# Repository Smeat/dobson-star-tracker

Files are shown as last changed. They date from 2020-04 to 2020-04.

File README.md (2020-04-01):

# dobson-star-tracker
This project aims to enable makers to motorize their dobson-style mounted telescopes using easily sourced hardware.

## Hardware

+ 2 Stepper Motors + drivers. I found that the size of my telescope (as pictured badly below) requires at least NEMA 17 with 1.2A current per phase. The altitude motor uses a (roughly) 5:1 gear ratio
+ Arduino with at least 6 Digital Pins. The instructions and example config work for an Arduino Mega with a RAMPS 1.4 shield
+ 3D printed motor mounts and gears
+ Optional: Two Buttons; Each requires one additional digital pin
+ Optional: A GPS module; Requires either a free TX/RX pin pair or two digital pins

## 3D Files

The printable files (stl and step format) can be found at: https://www.thingiverse.com/thing:3851307

## Installation

First of all, you will need the [Arduino IDE](https://www.arduino.cc/) and a few libraries:

* [TimerOne (on the Arduino Mega)](https://github.com/PaulStoffregen/TimerOne)
* [DueTimer (on the Arduino Due)](https://github.com/ivanseidel/DueTimer)
* [AccelStepper](https://www.airspayce.com/mikem/arduino/AccelStepper/)
* [FuGPS (should work without, if no GPS module is installed)](https://github.com/fu-hsi/FuGPS)
* [TimeLib](https://github.com/PaulStoffregen/Time)

Clone or download this repository and open the dobson-star-tracker.ino file in the Arduino IDE. The first thing you will need to set up are a few constants in the config.h file. Please read through the whole file and set everything according to your needs. When you initially build and upload the sketch without setting at least the `AZ_STEPS_PER_REV`and `ALT_STEPS_PER_REV` constants, the scope will not move since both of the values are set to 0. This is done to prevent the motors from moving unexpectedly and maybe damaging your telescope. Check the output of the Serial Monitor for more information. Initially, `DEBUG`, `DEBUG_SERIAL` and `DEBUG_STOP_ON_CONFIG_INSANITY` are enabled for useful output via the Serial Monitor. Once everything works correctly, you can disable them. For more information on how to connect the scope to Stellarium or how to use the display unit, check below.

## Connection to Stellarium

There are a few requisites for establishing a connection between the telescope and Stellarium.

### Arduino project
1. Set the `SERIAL_BAUDRATE` to 9600
2. Disable all of the DEBUG constants, so that the telescope does not send invalid commands to Stellarium. If Stellarium receives an invalid answer, it will wait for a few seconds before interacting with the telescope again. This either means, that it won't receive position updates from the telescope or that it won't send your commands. Setting a new position requires three commands sent by Stellarium. If one of them receives an invalid answer, Stellarium will not send the rest of the commands and your input will basically be ignored.
3. Close the Serial Monitor or Stellarium will not be able to connect to the telescope

### Settings in Stellarium
1. Open Stellarium and locate the "Telescope" tab. It should be in the lower control bar to the left of the time controls. If you can't find it, you may need to enable the "Telescope Control" plugin and restart Stellarium. Do so in the Configuration window in the last tab.
2. Click "Add" and set the following:
    * **Telescope controlled by:** "Stellarium, directly through a serial port"
    * **Name:** Choose one :)
    * **Connection delay:** Something around 0,1s, but should not matter too much
    * **Coordinate System:** J2000 (default)
    * **Start/Connect at startup:** Ticking the box means that Stellarium will try to connect to the telescope as soon as you open it. Use your preference.
    * **Serial port:** Select the same port as in your Arduino IDE
    * **Device Model:** Meade LX200 (compatible)
    * **Use field of view indicators:** Does not matter for controlling the telescope. Use your preference.
3. Confirm the settings with "OK"
4. Use "Start" to connect to the telescope
5. Wait a few seconds for it to show up on the screen and for it to settle down
6. The motors will not move until you align the telescope. To do so, follow this procedure:
   1. Choose your alignment star and select it in Stellarium
   2. Click "current object" in the telescope section
   3. Manually point the telescope at the selected star
   3. Confirm alignment by clicking "slew" and wait for the telescope on screen to point at the correct star
   4. The telescope is now aligned to that particular star and the stepper motors will be enabled
7. Now you can select a different star in Stellarium
8. Click "current object" in the telescope section
9. Click "slew" and watch the telescope move

## Wiring a RAMPS1.4

Wiring without the display unit

## Wiring with the Display Unit

My example uses a version of the well-known [RepRap Discount Full Graphics Smart Controller](https://reprap.org/wiki/RepRapDiscount_Full_Graphic_Smart_Controller). The only connection between the two Arduino boards is via the two cables connected to RX2 and TX2 on the Display Unit. For more information + code for the display unit head over to [ThisIsJustARandomGuy/telescope-display-unit/](https://github.com/ThisIsJustARandomGuy/telescope-display-unit/).

Wiring without the display unit

# Aligning using the display unit

If you have a display unit, you can use it to easily align the telescope. This works with/without Stellarium. To align the telescope when using a display unit, do the following:

1. Start the display unit and scope
2. Navigate to "Set Alignment" -> "Stars"
3. Look through the list and select a star that's visible in the sky
4. Once you click the star in the list, the motors of the telescope will turn off
5. Align the telescope to the star you have selected
6. Click again and confirm the alignment
7. The motors will turn on again and the telescope is now aligned.

## Serial Commands

+ :HLP# Print available Commands
+ Commands used by stellarium (you can use them as well)
  + :GR# Get Right Ascension
  + :GD# Get Declination
  + :Sr,HH:MM:SS# Set Right Ascension; Example: :Sr,12:34:56#
  + :Sd,[+/-]DD:MM:SS# Set Declination (DD is degrees) Example: :Sd,+12:34:56#
  + :MS# Start Move
  + :Q# Quit Move (Not Implemented)
+ Other commands
  + :TRK0# Disable tracking. This sets the telescopes isHomed member variable to false, so the motors stop moving
  + :TRK1# Enable tracking. The telescope will track whatever the target is
  + :STP0# Disable steppers permanently
  + :STP1# Enable steppers (after they were disabled using the STP0 command)
+ Debug commands
  + :DBGDSP# Send a status update to the display unit
  + :DBGDM[00-99]# Disable Motors for XX seconds
  + :DBGM[0-9]# Move to debug position X (see conversion.cpp; Later we will have a separate file with a star catalogue)
  + :DBGMIA# Increase Right Ascension by 1 degree
  + :DBGMDA# Decrease Right Ascension by 1 degree
  + :DBGMID# Increase Declination by 1 degree
  + :DBGMDD# Decrease Declination by 1 degree

## TODOs

The Most important TODOs are as follows (in no particular order)
+ Documentation
+ Equatorial Mounts: Adding equatorial mounts would be rather easy, but I don't own one so it's difficult to test. Maybe someone is interested in providing a PR?
+ Board compatibility: Out-of-the-box support for Arduino Mega and Arduino Due with their respective RAMPS shields (Mostly done, Mega + RAMPS 1.4 and Due + modified RAMPS 1.4 work)
+ Time keeping: Handle big swings which could happen due to GPS issues
+ EEPROM: Store time and location in EEPROM (Mega) or Flash (Due); Provide a simple API for doing so
+ Motor control: Turn On/Off permanently. Off for X seconds is already implemented as :DBGDM[00-99]#
+ SD card support: Loading a star atlas from a sd card (preferrably connected to the display unit, but direct connection should be possible too)

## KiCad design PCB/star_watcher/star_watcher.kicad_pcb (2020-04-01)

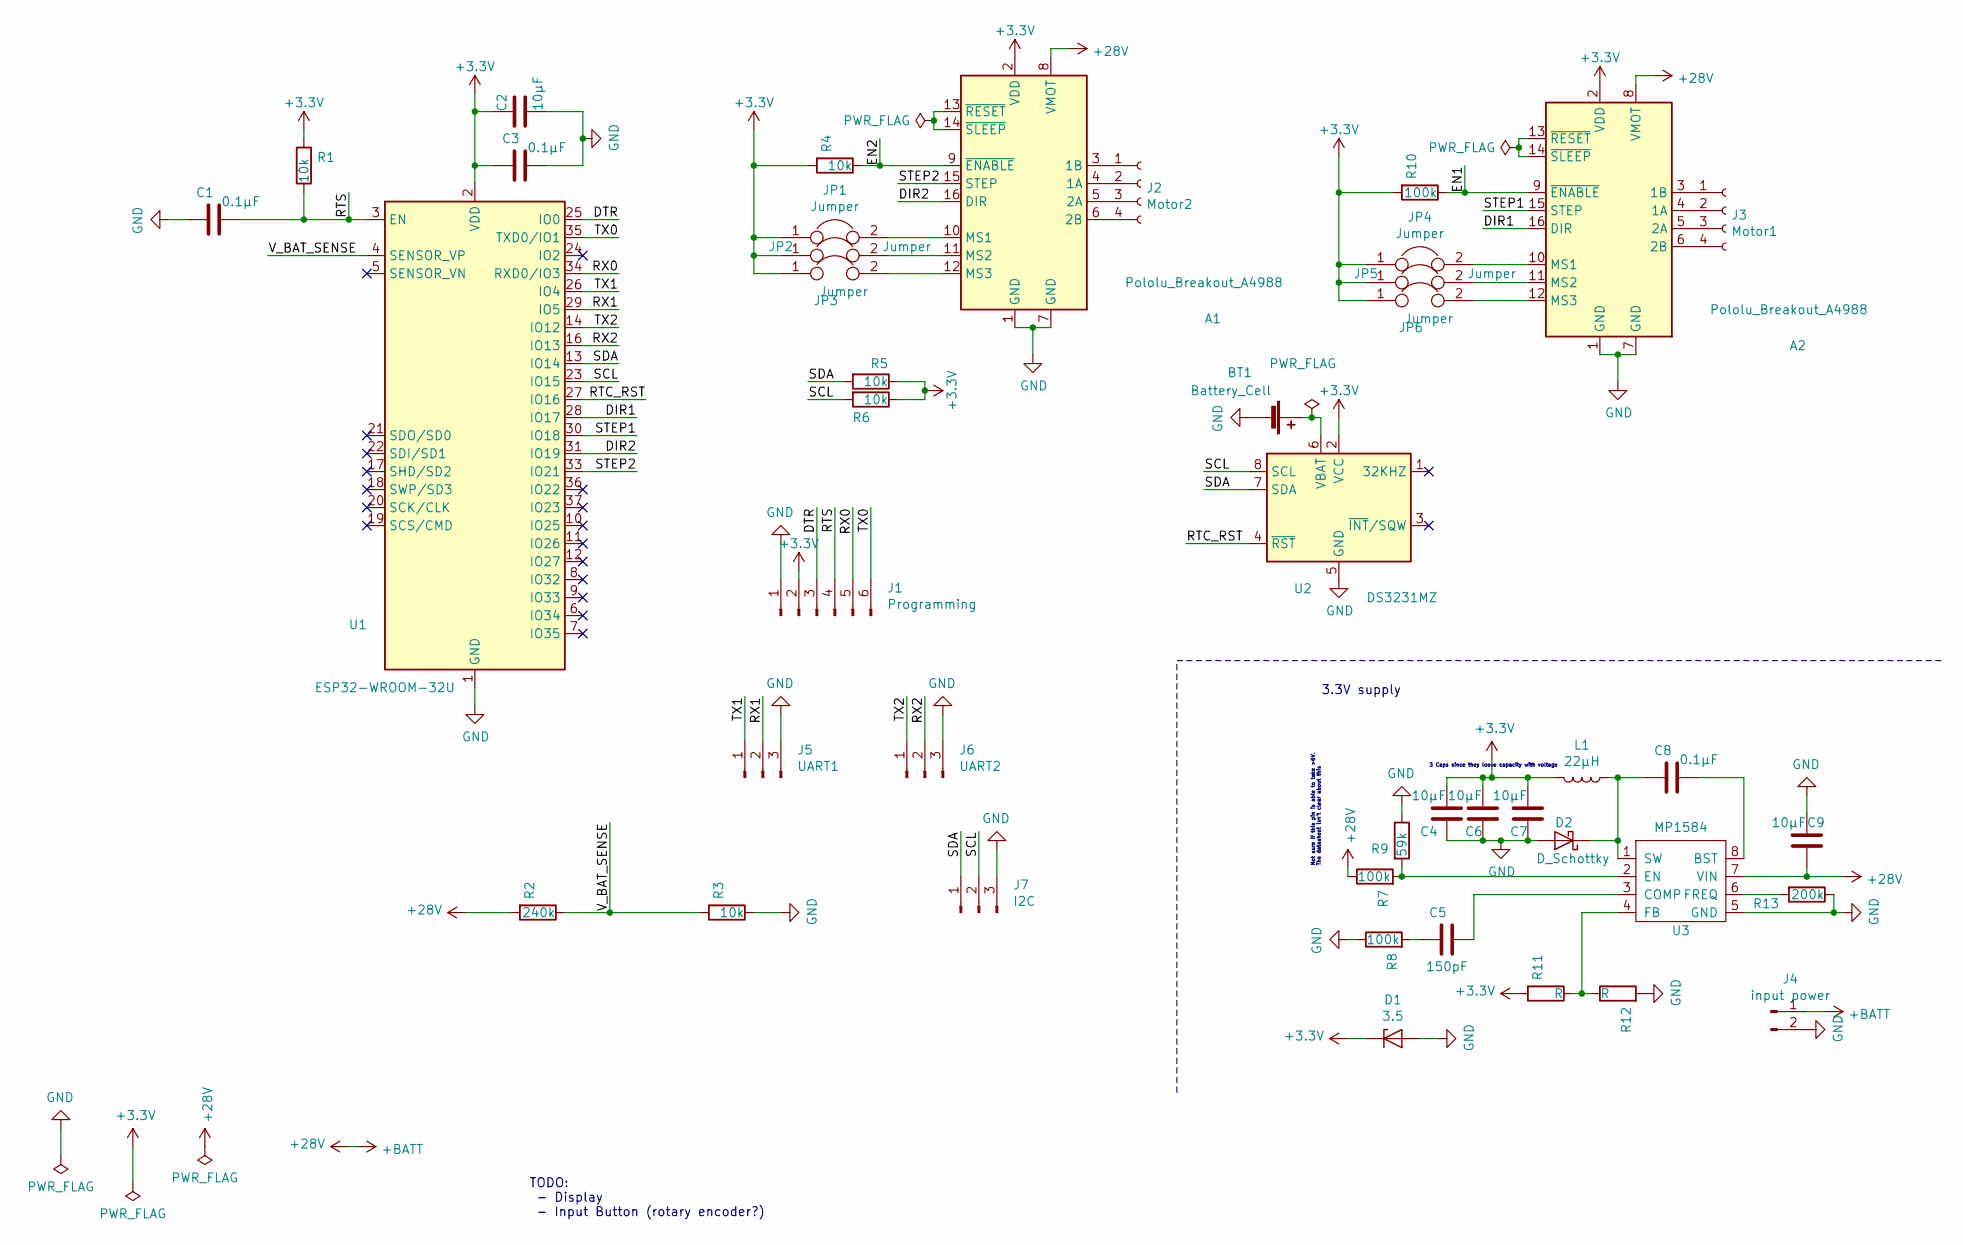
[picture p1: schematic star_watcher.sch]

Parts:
A1, A2: Pololu_Breakout_A4988; Pololu_Breakout-16_15.2x20.3mm
BT1: Battery_Cell; BatteryHolder_Keystone_103_1x20mm
C1, C3, C8: 0.1µF; C_0603_1608Metric
C2, C4, C6, C7, C9: 10µF; C_0805_2012Metric
C5: 150pF; C_0603_1608Metric
D1: 3.5; D_MELF
D2: D_Schottky; D_SMA
J1: Programming; PinHeader_1x06_P2.54mm_Vertical
J2: Motor2; PinHeader_1x04_P2.54mm_Vertical
J3: Motor1; PinHeader_1x04_P2.54mm_Vertical
J4: input power; SolderWirePad_1x02_P7.62mm_Drill2.5mm
J5: UART1; PinHeader_1x03_P2.54mm_Vertical
J6: UART2; PinHeader_1x03_P2.54mm_Vertical
J7: I2C; PinHeader_1x03_P2.54mm_Vertical
JP1, JP2, JP3, JP4, JP5, JP6: Jumper; PinHeader_1x02_P2.54mm_Vertical
L1: 22µH; L_12x12mm_H6mm
R1, R3, R4, R5, R6: 10k; R_0805_2012Metric
R2: 240k; R_0805_2012Metric
R7, R8, R10: 100k; R_0805_2012Metric
R9: 59k; R_0805_2012Metric
R11, R12: R; R_0805_2012Metric
R13: 200k; R_0805_2012Metric
U1: ESP32-WROOM-32U; ESP32-WROOM-32
U2: DS3231MZ; SOIC-8_3.9x4.9mm_P1.27mm
U3: MP1584; SOIC-8_3.9x4.9mm_P1.27mm

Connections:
+3V3: A1.2 (VDD), A2.2 (VDD), C2.1, C3.2, C4.2, C6.2, C7.2, D1.1 (K), J1.2, JP1.1, JP2.1, JP3.1, JP4.1, JP5.1, JP6.1, L1.2, R1.2, R4.2, R5.1, R6.1, R10.2, R11.2, U1.2 (VDD), U2.2 (VCC)
+28V: A1.8 (VMOT), A2.8 (VMOT), C9.1, J4.1, R2.2, R7.1, U3.7 (VIN)
/DIR1: A2.16 (DIR), U1.28 (IO17)
/DIR2: A1.16 (DIR), U1.31 (IO19)
/DTR: J1.3, U1.25 (IO0)
/EN1: A2.9 (~ENABLE), R10.1
/EN2: A1.9 (~ENABLE), R4.1
/RTC_RST: U1.27 (IO16), U2.4 (~RST)
/RTS: C1.1, J1.4, R1.1, U1.3 (EN)
/RX0: J1.5, U1.34 (RXD0/IO3)
/RX1: J5.2, U1.29 (IO5)
/RX2: J6.2, U1.16 (IO13)
/SCL: J7.2, R6.2, U1.23 (IO15), U2.8 (SCL)
/SDA: J7.1, R5.2, U1.13 (IO14), U2.7 (SDA)
/STEP1: A2.15 (STEP), U1.30 (IO18)
/STEP2: A1.15 (STEP), U1.33 (IO21)
/TX0: J1.6, U1.35 (TXD0/IO1)
/TX1: J5.1, U1.26 (IO4)
/TX2: J6.1, U1.14 (IO12)
/V_BAT_SENSE: R2.1, R3.2, U1.4 (SENSOR_VP)
GND: A1.1 (GND), A1.7 (GND), A2.1 (GND), A2.7 (GND), BT1.2 (-), C1.2, C2.2, C3.1, C4.1, C6.1, C7.1, C9.2, D1.2 (A), D2.2 (A), J1.1, J4.2, J5.3, J6.3, J7.3, R3.1, R8.1, R9.1, R12.2, R13.1, U1.1 (GND), U1.15 (GND), U1.38 (GND), U1.39 (GND), U2.5 (GND), U3.5 (GND)
unnamed: A1.3 (1B), J2.1
unnamed: A1.4 (1A), J2.2
unnamed: A1.5 (2A), J2.3
unnamed: A1.6 (2B), J2.4
unnamed: A1.10 (MS1), JP1.2
unnamed: A1.11 (MS2), JP2.2
unnamed: A1.12 (MS3), JP3.2
unnamed: A1.13 (~RESET), A1.14 (~SLEEP)
unnamed: A2.3 (1B), J3.1
unnamed: A2.4 (1A), J3.2
unnamed: A2.5 (2A), J3.3
unnamed: A2.6 (2B), J3.4
unnamed: A2.10 (MS1), JP4.2
unnamed: A2.11 (MS2), JP5.2
unnamed: A2.12 (MS3), JP6.2
unnamed: A2.13 (~RESET), A2.14 (~SLEEP)
unnamed: BT1.1 (+), U2.6 (VBAT)
unnamed: C5.1, U3.3 (COMP)
unnamed: C5.2, R8.2
unnamed: C8.1, U3.8 (BST)
unnamed: C8.2, D2.1 (K), L1.1, U3.1 (SW)
unnamed: R7.2, R9.2, U3.2 (EN)
unnamed: R11.1, R12.1, U3.4 (FB)
unnamed: R13.2, U3.6 (FREQ)

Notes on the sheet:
Not sure if this pin is able to take >6V. The datasheet isn't clear about this
3 Caps since they loose capacity with voltage
3.3V supply
TODO: - Display - Input Button (rotary encoder?)

Board: 2 copper layers, 44 parts (4 on the bottom side), 45 nets, no tracks yet.

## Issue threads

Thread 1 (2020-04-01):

TODO

Smeat, 2020-04-01:
- [ ] Add interface for getting gps/time from phone via bluetooth/wifi
- [ ] Connection to Stellarium and KStars via wifi
- [x] Schematic
  -  [X] Find a display with red background light
     - The LEDs on the Nokia 5110 LCD can easily be replaced
  -  [ ] SD support for saving star maps
   - [ ] Implement filesystem or use a faster fat lib
      - Fat reads were at 0.5MB/s. RAW at 7MB/s
         - SIMBAD library for Vmag <11 is about 16mb for the data and 30mb for the names
      - [ ] UI for selecting targets, calibrating etc
- [ ]  Actually get the hardware and test it

Smeat, 2020-04-11:
Using another project: https://github.com/Smeat/Star_Tracker

Closed 2020-04-11.

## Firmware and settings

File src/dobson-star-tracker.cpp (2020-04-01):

#include <TimeLib.h>
#include <AccelStepper.h>
#include <Arduino.h>
#include <HardwareSerial.h>
#include <MultiStepper.h>

#include "config.h"
#include "conversion.h"
//#include "location.h"

//Load the timer library, depending on the selected BOARD_TYPE
#ifdef BOARD_ARDUINO_MEGA
	#include <TimerOne.h>
#elif defined BOARD_ARDUINO_DUE
	#include <DueTimer.h>
#endif

// Load the display unit if it's enabled
#ifdef SERIAL_DISPLAY_ENABLED
#include "display_unit.h"
#endif

// Load the required observer class
#ifdef GPS_FIXED_POS
	#include "./FixedObserver.h"
#else
	#include "./GpsObserver.h"
#endif

// Include the mount, depending on the selected MOUNT_TYPE
#ifdef MOUNT_TYPE_DOBSON
	#include "./Dobson.h"
#elif defined MOUNT_TYPE_EQUATORIAL
	#include "./Equatorial.h" // NOT IMPLEMENTED!
#elif defined MOUNT_TYPE_DIRECT
	#include "./DirectDrive.h"
#endif


// Initialize the Steppers
AccelStepper azimuth(AccelStepper::DRIVER, AZ_STEP_PIN, AZ_DIR_PIN);    // Azimuth stepper
AccelStepper altitude(AccelStepper::DRIVER, ALT_STEP_PIN, ALT_DIR_PIN); // Altitude stepper

// Initialize the Observer (either fixed or GPS)
#ifdef GPS_FIXED_POS
	FixedObserver observer(ALT, LAT, LNG, INITIAL_YEAR, INITIAL_MONTH, INITIAL_DAY, INITIAL_HOUR, INITIAL_MINUTE, INITIAL_SECOND);
#else
	GpsObserver observer;
#endif

// Initialize the Mount
#ifdef MOUNT_TYPE_DOBSON
	Dobson scope(azimuth, altitude, observer);
#elif defined MOUNT_TYPE_EQUATORIAL
	Equatorial scope(azimuth, altitude, observer); // NOT IMPLEMENTED!
#elif defined MOUNT_TYPE_DIRECT
	DirectDrive scope(azimuth, altitude, observer);
#endif

// Are the stepper drivers currently enabled?
bool motorsEnabled = false;

// This increases every loop iteration and resets at 10.000
unsigned int loopIteration = 0;

// Is the loop() function being run for the first time?
bool first_loop_run = true;

// millis() at the time of the latest call to Mount::calculateMotorTargets()
long last_motor_update = 0;

#ifdef DEBUG_HOME_IMMEDIATELY
	const bool homeImmediately = true;
#else
	const bool homeImmediately = false;
#endif


/**
 * Motor Interrupt handler
 * This is attached to timer interrupt 1. It gets called every STEPPER_INTERRUPT_FREQ / 1.000.000 seconds and moves our steppers
 */
void moveSteppers() {
	azimuth.run();
	altitude.run();
}


/**
 * Initialize stepper drivers. Sets pin inversion config, max speed and acceleration per stepper
 */
void setupSteppers() {
	// Set stepper pins
	pinMode(AZ_ENABLE_PIN, OUTPUT);  // Azimuth pin
	pinMode(ALT_ENABLE_PIN, OUTPUT); // Altitude pin

	azimuth.setPinsInverted(true, false, false);
	azimuth.setMaxSpeed(AZ_MAX_SPEED);
	azimuth.setAcceleration(AZ_MAX_ACCEL);

	altitude.setPinsInverted(true, false, false);
	altitude.setMaxSpeed(ALT_MAX_SPEED);
	altitude.setAcceleration(ALT_MAX_ACCEL);

	// Setup the stepper interrupt. Depends on the selected board
#ifdef BOARD_ARDUINO_MEGA
	Timer1.initialize(STEPPER_INTERRUPT_FREQ);
	Timer1.attachInterrupt(&moveSteppers);
#elif defined BOARD_ARDUINO_DUE
	Timer.getAvailable()
		.attachInterrupt(&moveSteppers)
		.start(STEPPER_INTERRUPT_FREQ);
#elif defined(BOARD_ESP32)
	hw_timer_t * timer = NULL;
	// Use 1st timer of 4 (counted from zero).
	// Set 80 divider for prescaler (see ESP32 Technical Reference Manual for more
	// info).
	timer = timerBegin(0, 80, true);

	// Attach onTimer function to our timer.
	timerAttachInterrupt(timer, &moveSteppers, true);

	// Set alarm to call onTimer function every second (value in microseconds).
	// Repeat the alarm (third parameter)
	timerAlarmWrite(timer, STEPPER_INTERRUPT_FREQ, true);

	// Start an alarm
	timerAlarmEnable(timer);
#endif

	DEBUG_PRINT("  Steppers enabled:  ");
#ifdef AZ_ENABLE
	DEBUG_PRINT("Az=ON");
#else
	DEBUG_PRINT("Az=OFF");
#endif

#ifdef ALT_ENABLE
	DEBUG_PRINTLN("  Alt=ON");
#else
	DEBUG_PRINTLN("  Alt=OFF");
#endif
} // setupSteppers


/*
 * This function turns stepper motor drivers on, if these conditions are met:
 * STEPPERS_ON_PIN reads HIGH
 * operating mode is not Mode::INITIALIZING
 * TODO Maybe the conditions need to change (esp. the opmode one)
 */
void setSteppersOnOffState() {
	const bool isTracking = scope.getMode() == Mode::TRACKING;

#ifdef STEPPERS_ON_PIN
	// If the STEPPERS_ON switch is installed, check its state
	const bool steppersSwitchOn = digitalRead(STEPPERS_ON_PIN) == HIGH;
#else
	// If no STEPPERS_ON switch is installed, define its state as enabled
#define steppersSwitchOn true
#endif

	if (steppersSwitchOn && isTracking) {
		// Motors on
		motorsEnabled = true;
#ifdef AZ_ENABLE
		digitalWrite(AZ_ENABLE_PIN, LOW);
#endif
#ifdef ALT_ENABLE
		digitalWrite(ALT_ENABLE_PIN, LOW);
#endif
	}
	else {
		// Motors OFF
		motorsEnabled = false;
#ifdef AZ_ENABLE
		digitalWrite(AZ_ENABLE_PIN, HIGH);
#endif
#ifdef ALT_ENABLE
		digitalWrite(ALT_ENABLE_PIN, HIGH);
#endif
	}
}

#ifndef REMOVE_SPLASH
	void greet() {
		DEBUG_PRINTLN("                      __          __  _                          ");
		DEBUG_PRINTLN("                      \\ \\        / / | |                         ");
		DEBUG_PRINTLN("                       \\ \\  /\\  / /__| | ___ ___  _ __ ___   ___ ");
		DEBUG_PRINTLN("                        \\ \\/  \\/ / _ \\ |/ __/ _ \\| '_ ` _ \\ / _ \\");
		DEBUG_PRINTLN("                         \\  /\\  /  __/ | (_| (_) | | | | | |  __/");
		DEBUG_PRINTLN("                          \\/  \\/ \\___|_|\\___\\___/|_| |_| |_|\\___|");
		DEBUG_PRINTLN("                                                                 ");

		DEBUG_PRINTLN(" _____        _                          _____ _                _______             _             ");
		DEBUG_PRINTLN("|  __ \\      | |                        / ____| |              |__   __|           | |            ");
		DEBUG_PRINTLN("| |  | | ___ | |__  ___  ___  _ __     | (___ | |_ __ _ _ __      | |_ __ __ _  ___| | _____ _ __ ");
		DEBUG_PRINTLN("| |  | |/ _ \\| '_ \\/ __|/ _ \\| '_ \\     \\___ \\| __/ _` | '__|     | | '__/ _` |/ __| |/ / _ \\ '__|");
		DEBUG_PRINTLN("| |__| | (_) | |_) \\__ \\ (_) | | | |    ____) | || (_| | |        | | | | (_| | (__|   <  __/ |   ");
		DEBUG_PRINTLN("|_____/ \\___/|_.__/|___/\\___/|_| |_|   |_____/ \\__\\__,_|_|        |_|_|  \\__,_|\\___|_|\\_\\___|_|   ");
		DEBUG_PRINTLN("                                                                                               ");

		DEBUG_PRINTLN("Welcome to the dobson-star-tracker serial console.");
		DEBUG_PRINTLN("Before continuing, please set up the config.h file.");
		DEBUG_PRINTLN("Type :HLP# and press Enter to see a list of available commands");
		DEBUG_PRINTLN();
		DEBUG_PRINTLN();
		DEBUG_PRINTLN();
	}
#endif


/**
 * Performs a few sanity checks on the config. If there are any obvious errors,
 * warn the user. Depending on what is set in config.h this may enter an
 * endless loop to prevent damage to the telescope hardware. Have a look at
 * DEBUG_STOP_ON_CONFIG_INSANITY in config.h
 */
void config_sanity_check() {
	bool failed = false;
	bool can_continue = true;

	// Begin checks
	if (AZ_STEPS_PER_REV <= 0) {
		DEBUG_PRINTLN("  Warning: AZ_STEPS_PER_REV should probably be > 0");
		failed = true;
	}
	if (ALT_STEPS_PER_REV <= 0) {
		DEBUG_PRINTLN("  Warning: ALT_STEPS_PER_REV should probably be > 0");
		failed = true;
	}

	#if defined BUZZER_PIN
		#if BUZZER_PIN == STEPPERS_ON_PIN
			DEBUG_PRINTLN("  Error: BUZZER_PIN and STEPPERS_ON_PIN are set to the same pin number.");
			failed = true; can_continue = false;
		#endif
		#if BUZZER_PIN == HOME_NOW_PIN
			DEBUG_PRINTLN("  Error: BUZZER_PIN and HOME_NOW_PIN are set to the same pin number.");
			failed = true; can_continue = false;
		#endif
		#if BUZZER_PIN == TARGET_SELECT_PIN
			DEBUG_PRINTLN("  Error: BUZZER_PIN and TARGET_SELECT_PIN are set to the same pin number.");
			failed = true; can_continue = false;
		#endif
	#endif

	#if defined STEPPERS_ON_PIN
		#if STEPPERS_ON_PIN == HOME_NOW_PIN
			DEBUG_PRINTLN("  Error: STEPPERS_ON_PIN and HOME_NOW_PIN are set to the same pin number.");
			failed = true; can_continue = false;
		#endif
		#if STEPPERS_ON_PIN == TARGET_SELECT_PIN
			DEBUG_PRINTLN("  Error: STEPPERS_ON_PIN and TARGET_SELECT_PIN are set to the same pin number.");
			failed = true; can_continue = false;
		#endif
	#endif

	#if defined HOME_NOW_PIN && HOME_NOW_PIN == TARGET_SELECT_PIN
		DEBUG_PRINTLN("  Error: HOME_NOW_PIN and TARGET_SELECT_PIN are set to the same pin number.");
		failed = true; can_continue = false;
	#endif

	#ifndef GPS_FIXED_POS
		#if GPS_MIN_SATELLITES <= 0
			DEBUG_PRINTLN("  Warning: GPS_MIN_SATELLITES should probably be > 0");
			failed = true;
		#endif

		#if GPS_MIN_SATELLITES_TIME <= 0
			DEBUG_PRINTLN("  Warning: GPS_MIN_SATELLITES_TIME should probably be > 0");
			failed = true;
		#endif
	#endif

	#if UPDATE_MOTOR_POS_MS <= 0
		DEBUG_PRINTLN("  Warning: UPDATE_MOTOR_POS_MS should probably be > 0");
		failed = true;
	#endif
		

	#if STEPPER_INTERRUPT_FREQ <= 0
		DEBUG_PRINTLN("  Warning: STEPPER_INTERRUPT_FREQ should probably be > 0");
		failed = true;
	#endif

	// End checks

	if (failed) {
		DEBUG_PRINTLN("  Config sanity check has failed.");
		DEBUG_PRINTLN("  Check the output above for errors and review config.h");
		DEBUG_PRINTLN("  Do not continue until you know why this message appeared!");
		#ifdef DEBUG_STOP_ON_CONFIG_INSANITY
			bool stop = true;
			while (stop) {
				// Buzzer is installed. Start buzzing and continue endless loop
				#ifdef BUZZER_PIN
					digitalWrite(BUZZER_PIN, HIGH);
				#endif

				// DEBUG_SERIAL is enabled. Wait for "ok" input
				#ifdef DEBUG_SERIAL
					DEBUG_PRINTLN("  Press 1 and Enter to continue");
					while (!Serial.available()) {}
					if (Serial.read() == '1') {
						if (can_continue) {
							stop = false;
						}
						else {
							DEBUG_PRINTLN("  I'm sorry Dave, I'm afraid I can't do that. Please fix the errors first");
						}
					}
				#endif
			}
			// Buzzer is installed. Stop buzzing after the continue command
			#ifdef BUZZER_PIN
				digitalWrite(BUZZER_PIN, LOW);
			#endif
		#endif
	}
}

/**
 * Run various tasks required to initialize the following:
 * Serial connection
 * Serial communication
 * Stepper motors
 * If enabled:
 *     Display module
 *     GPS module
 *     Buzzer
 *     Steppers On/Off Button
 *     Home Now Button
 *     Target Select Button
 *
 * Finally, telescope.initialize() is called. This sets an initial target (depending on the MOUNT_TYPE) and the initial scope operating mode
 */
void setup() {
	Serial.begin(SERIAL_BAUDRATE);
	#if defined DEBUG && defined DEBUG_SERIAL
		delay(500);
		#ifndef REMOVE_SPLASH
			greet();
		#endif
	#endif
			delay(500);
	DEBUG_PRINTLN("> Performing config sanity check");
	config_sanity_check();
	
	// If the serial display is enabled, begin communicating with it
	#ifdef SERIAL_DISPLAY_ENABLED
		DEBUG_PRINT("> Initializing Display module ... ");
		initDisplayCommunication(scope);
		DEBUG_PRINTLN("done");
	#else
		DEBUG_PRINTLN("Display module is disabled");
	#endif

	DEBUG_PRINT("> Initializing Observer module ... ");
	// This initializes the Observer (including the GPS module, if required)
	observer.initialize();
	DEBUG_PRINTLN("done");
	#if defined DEBUG && defined DEBUG_SERIAL
		observer.printDebugInfo();
	#endif

	DEBUG_PRINTLN("> Initializing Telescope module ... ");
	// Initialize the telescope
	scope.initialize();

	DEBUG_PRINTLN();
	DEBUG_PRINTLN("> Initializing Serial communications module ... ");
	// This sets up communication with Stellarium / Serial console
	initCommunication(scope);

	DEBUG_PRINTLN();
	DEBUG_PRINTLN("> Initializing Stepper drivers ... ");
	// Initialize stepper motor drivers
	setupSteppers();

	DEBUG_PRINTLN("> Initializing Buttons and Output ... ");
	DEBUG_PRINT("    Buzzer...............");
	// Button pins
	#ifdef BUZZER_PIN
		pinMode(BUZZER_PIN, OUTPUT);
		digitalWrite(BUZZER_PIN, HIGH);
		//delay(1000);
		digitalWrite(BUZZER_PIN, LOW);
		DEBUG_PRINLN("done");
	#else
		DEBUG_PRINTLN("not connected");
	#endif

	DEBUG_PRINT("    Steppers on/off......");
	// Steppers on/off switch
	#ifdef STEPPERS_ON_PIN
		pinMode(STEPPERS_ON_PIN, INPUT);
		DEBUG_PRINLN("done");
	#else
		DEBUG_PRINTLN("not connected");
	#endif


	DEBUG_PRINT("    Home now.............");
	// Home now switch
	#ifdef HOME_NOW_PIN
		pinMode(HOME_NOW_PIN, INPUT);

		DEBUG_PRINLN("done");
	#else
		DEBUG_PRINTLN("not connected");
	#endif


	DEBUG_PRINT("    Debug target.........");
	// Target select pin
	#ifdef TARGET_SELECT_PIN
		// Input mode for the select pin is INPUT with PULLUP enabled, so that we can use a longer cable
		pinMode(TARGET_SELECT_PIN, INPUT_PULLUP);
		DEBUG_PRINLN("done");
	#else
		DEBUG_PRINTLN("not connected");
	#endif

	// If the serial display is enabled, send the telescope status
	#ifdef SERIAL_DISPLAY_ENABLED
		DEBUG_PRINTLN("> Sending status to Display .... ");
		display_statusUpdate(scope);
	#endif

	DEBUG_PRINTLN("> Initialization done");
	DEBUG_PRINTLN();
	DEBUG_PRINTLN();
	DEBUG_PRINTLN();

}


/*
 * Main program loop. It does roughly the following (in order)
 * 1) Check whether the Home Button is pressed. If so, set the scope back to homing mode
 * 2) Get updates from the GPS module and tell the telescope instance about it
 * 3) Handle communication over serial
 * 4) Check whether homing mode should end (TODO This should move to the telescope class)
 * 5) Turn the stepper drivers on/off
 * 6) Every 10.000 loop iterations:
 *    - Run the necessary calculations to update the telescope target position
 *    - Update the target values for the steppers
 * 7) Debug communications, if enabled
*/
void loop() {
	#ifdef HOME_NOW_PIN
		// If the HOME button is installed and pressed/switched on start homing mode
		const bool currentlyAligning = digitalRead(HOME_NOW_PIN) == HIGH;

		if (currentlyAligning) {
			// The telescope stands still and waits for the next target selection (which it then assumes it is pointing at)
			// Setting homed to false also sets the telescope to operating mode Mode::ALIGNING
			scope.setHomed(false);
		}
	#else
		// If no HOME button exists, it never gets pressed, so we define it as false
		#define currentlyAligning false
	#endif

	// Get the current position from our GPS module. If no GPS is installed
	// or no fix is available values from EEPROM / config.h are used.
	// For more details look at the implementations of the Observer class
	observer.updatePosition();

	// Handle serial serial communication. Returns true if homing was just performed
	bool justAligned = handleSerialCommunication(scope, observer);

	#ifdef SERIAL_DISPLAY_ENABLED
		handleDisplayCommunication(scope, observer);
	#endif

	// If DEBUG_HOME_IMMEDIATELY is defined, homing is performed on first loop iteration.
	// Otherwise a serial command or HOME_NOW Button are required
	if (justAligned || currentlyAligning
		|| (homeImmediately && loopIteration == 0)) {
		justAligned = true;

		// Sets the telescope to operating mode Mode::TRACKING
		scope.setHomed(true);
	}

	// Turn the stepper motors on or off, depending on state of STEPPERS_ON_PIN
	setSteppersOnOffState();

	// Every UPDATE_MOTOR_POS_MS milliseconds, or when this is run the first time, 
	// we calculate and update the target motor position of the telescope
	if (millis() - last_motor_update >= UPDATE_MOTOR_POS_MS || first_loop_run) {
		first_loop_run = false;
		last_motor_update = millis();

		#if defined(DEBUG) && defined(DEBUG_SERIAL_STEPPER_MOVEMENT) && defined(DEBUG_TIMING)
			// Start timing the calculation
			long micros_start = micros();
		#endif

		// This function converts the coordinates
		scope.calculateMotorTargets();

		// This actually makes the motors move to their desired target positions
		#ifdef MOUNT_STOP_UNTIL_GPS_POS_VALID
			if (observer.hasValidPosition()) {
				scope.move();
			}
		#else
			scope.move();
		#endif

		#if defined(DEBUG) && defined(DEBUG_SERIAL_STEPPER_MOVEMENT) && defined(DEBUG_TIMING)
			// Debug: If a move took place, output how long it took from beginning to end of the calculation
			if (scope._didMove) {
				long calc_time = scope._lastCalcMicros - micros_start;
				long dbg_time = micros() - scope._lastCalcMicros;
				DEBUG_PRINT("; Calc: ");
				DEBUG_PRINT(calc_time / 1000.);
				DEBUG_PRINT("ms; DbgComms: ");
				DEBUG_PRINT(dbg_time / 1000.);
				DEBUG_PRINTLN("ms");
			}
		#endif
	}

	loopIteration++;
}

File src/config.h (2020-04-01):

#pragma once

/*
 * Board type
 * Uncomment only one of these, depending on the board you are running the firmware on
 */
//#define BOARD_ARDUINO_MEGA
//#define BOARD_ARDUINO_DUE

// Baudrate to use when communicating over serial connection
#define SERIAL_BAUDRATE 56000

/*
 * Mount type
 * The default is "Direct Drive". Please see notes below for why
 * 
 * This setting defines which motion system is used by the telescope. Currently, there are three planned, and two supported mount systems:
 * Dobson, Equatorial (NOT IMPLEMENTED!), Direct Drive
 * You can find more information about Dobson on Equatorial mounts here: https://science.howstuffworks.com/telescope5.htm
 * 
 * Notes on the Direct Drive "mount"
 *    Directly moves the steppers to the provided angles without any coordinate system conversion
 *    Does NOT TRACK
 *    It's useful to see whether the axes are set up correctly (connection, direction and steps per revolution)
 *    Because it doesn't track, it won't get confused by unreliable times/GPS positions
 *    If you're using a Dobson mount, but are exclusively controlling it with a Joystick/IR Remote (NOT IMPLEMENTED) this appears to be the most intuitive control method. Others will work as well, though.
 * 
 * IMPORTANT: Define the same mount type on the display, if you are using it.
 * If you're using the wrong combination, the display unit should show a warning, but still allow you to change the angles.
 * The telescope will, at the least, not be able to point to the correct location if you select the wrong mount type on either the display unit or here.
 */
#define MOUNT_TYPE_DOBSON     // Target should be in Ra/Dec. Supports tracking
//#define MOUNT_TYPE_EQUATORIAL // NOT IMPLEMENTED! Target should be in Ra/Dec. Supports tracking
//#define MOUNT_TYPE_DIRECT       // Target should be in degrees for both axis1 and axis2. Does NOT support tracking

/*
 * Azimuth Stepper
 * Direct Drive: Axis 1
 * Dobson: Azimuth (horizontal) axis
 * Equatorial: Not implemented; Right ascension
 */
#define AZ_ENABLE_PIN       38     // RAMPS 1.4 X stepper
#define AZ_STEP_PIN         54     // RAMPS 1.4
#define AZ_DIR_PIN          55     // RAMPS 1.4
#define AZ_STEPS_PER_REV     0.    // My value: 119467.0  // How many steps the stepper motor needs to complete for one a horizontal 360degree revolution of the telescope (my setup: 3200 : 1 and 560 : 15)
#define AZ_MAX_ACCEL        300    // Maximum acceleration for the azimuth stepper
#define AZ_MAX_SPEED       4000    // Maximum speed for the azimuth stepper

/*
 * Altitude stepper
 * Direct Drive: Axis 2
 * Dobson: Altitude (vertical) axis
 * Equatorial: Not implemented; Declination axis
 */
#define ALT_ENABLE_PIN       56     // RAMPS 1.4 Y stepper
#define ALT_STEP_PIN         60     // RAMPS 1.4
#define ALT_DIR_PIN          61     // RAMPS 1.4
#define ALT_STEPS_PER_REV     0.    // How many steps the stepper motor needs to complete for a vertical 360degree revolution of the telescope (my setup: 5.18:1 and 3200 : 1 and 105 : 12 = 147840.0)
#define ALT_MAX_ACCEL         400   // Maximum acceleration for the altitude stepper
#define ALT_MAX_SPEED        10000  // Maximum speed for the altitude stepper

#define AZ_STEPS_PER_DEG   (AZ_STEPS_PER_REV / 360.0)
#define ALT_STEPS_PER_DEG  (ALT_STEPS_PER_REV / 360.0)

/*
 * Control via Display
 * The DirectDrive telescope can be controlled via an Arduino+Display unit connected via serial port.
 * Eventually, I hope to get the Dobson one working as well
 */
#define SERIAL_DISPLAY_ENABLED              // Uncomment this line to enable/disable control via the display unit
#define SERIAL_DISPLAY_PORT Serial1			// Which Serial port to use. Serial 2 is 16(RX) and 17(TX) on the Mega/Due or 
#define SERIAL_DISPLAY_BAUDRATE       9600  // The baudrate which is used to communicate with the display unit. On the display unit SERIAL_BAUDRATE must have the same value

/*
 * Other Pins
 * Attention: These only apply to my setup. Best to disable all of them and add them back one by one.
 *
 * Comments for myself:
 * y+ is dead
 * y- buzzer
 * x+ stepper on
 * x- pushbutton
 */
//#define BUZZER_PIN      14  // Uncomment if you have a buzzer installed. Default pin for RAMPS 1.4 is Y_MIN
//#define STEPPERS_ON_PIN    3  // Uncomment if you have a stepper switch installed. Default pin for RAMPS 1.4 is  X_MIN. If this pin is HIGH, the steppers are turned on.
//#define HOME_NOW_PIN     3  // Uncomment if you have a homing mode switch installed. Default pin for RAMPS 1.4 is X_MAX. If this pin is HIGH, Telescope::setHomed(true) is called. Ignored when using MOUNT_TYPE_DIRECT
//#define TARGET_SELECT_PIN  2  // Debug button which cycles through a few different targets

/**
 * ----------------
 * Debug section
 * Use settings in this section to set up your telescope.
 * You can speed up time, enable debug messages over serial etc.
 * ----------------
 */
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

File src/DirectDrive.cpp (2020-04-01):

#include <AccelStepper.h>
#include <Time.h>

#include "./config.h"
#include "./location.h"
#include "./Observer.h"

#include "./DirectDrive.h"


DirectDrive::DirectDrive(AccelStepper& azimuthStepper, AccelStepper& altitudeStepper, Observer &observer) :
	_azimuthStepper(azimuthStepper), _altitudeStepper(altitudeStepper), _observer(observer) {
}

void DirectDrive::initialize() {
	// This mount type does not actually track, but it is still
	// required by some other parts of the firmware to have tracking mode enabled
	setMode(Mode::ALIGNING);

	// The initial setting is 0 degrees for both axes
	setTarget({ 0, 0 });
}

// Calculate new motor targets. This does not yet execute the move
void DirectDrive::calculateMotorTargets() {
	// The only conversion that's needed is degrees to motor steps
	_steppersTarget.azimuth = (long)(_target.rightAscension * AZ_STEPS_PER_DEG);
	_steppersTarget.altitude = (long)(_target.declination * ALT_STEPS_PER_DEG);
	
	#ifdef DEBUG_TIMING
		_lastCalcMicros = micros();
	#endif
}

void DirectDrive::setAlignment(RaDecPosition alignment) {
	// Set the steppers to the target position
	_azimuthStepper.setCurrentPosition((long)(alignment.rightAscension * AZ_STEPS_PER_DEG));
	_altitudeStepper.setCurrentPosition((long)(alignment.declination * ALT_STEPS_PER_DEG));
	setTarget(alignment);
}


/*
 * This method gets executed every 10.000 loop iterations right after Dobson::calculateMotorTargets() was called.
 * It checks whether the telescope is homed. If it is NOT homed, it sets the target as its current motor positions and sets _isHomed to true.
 * The next time the method gets called, _isHomed is true , and the stepper motors are actually moved to their new required position.
 */
void DirectDrive::move() {
	if ((millis() < 5000)) {
		DEBUG_PRINTLN("Ignore move for first 5 seconds");
		return;
	}

	// Move the steppers to their target positions
	_azimuthStepper.moveTo(_steppersTarget.azimuth);
	_altitudeStepper.moveTo(_steppersTarget.altitude);

	_currentPosition = {
		_target.rightAscension,
		_target.declination
	};

	// TODO Update this correctly
	_didMove = true;

	#if defined(DEBUG_SERIAL_STEPPER_MOVEMENT_VERBOSE) || defined(DEBUG_SERIAL_STEPPER_MOVEMENT)
		if (_didMove) {
			DEBUG_PRINTLN("-------------------------------------------------------------------------------------------------------------------");
			DEBUG_PRINT("Desired:     ");

			DEBUG_PRINT("Ra/Dec ");
			DEBUG_PRINT(_target.rightAscension);
			DEBUG_PRINT("° / ");
			DEBUG_PRINT(_target.declination);
			DEBUG_PRINT("°");

			DEBUG_PRINT("   Actual Steps ");
			DEBUG_PRINT(_azimuthStepper.currentPosition());
			DEBUG_PRINT("s / ");
			DEBUG_PRINT(_altitudeStepper.currentPosition());
			DEBUG_PRINT("s");

			#ifndef DEBUG_TIMING
				DEBUG_PRINTLN("");
			#endif
		}
	#endif
}

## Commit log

2020-04-01 Add platformio and esp32 support Totatlly untested and awful, but compiles ;)
2020-04-01 Add first draft for a pcb
    [star_watcher.kicad_pcb, star_watcher.sch]
2020-04-02 PCB should be feature complete now Just a few capacitors and startup IO stuff missing.
    [star_watcher.sch]
2020-04-03 Use nokia 5110 as display
    [star_watcher.sch]
